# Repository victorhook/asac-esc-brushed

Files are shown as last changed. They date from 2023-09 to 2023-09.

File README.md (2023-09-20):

# **A** **S**imple **A**nd **C**ool brushed ESC
Why do cool fpv drones pretty much always use brushless motors? Well, because they are really good. BUT, they are quite expensive, and brushless ESCs are also quite expensive, since they require somewhat complex hardware and firmware. Thus, this project aims to make a simple and cool ESC that can be used for drones with *brushed* motors. Let's see how this goes!

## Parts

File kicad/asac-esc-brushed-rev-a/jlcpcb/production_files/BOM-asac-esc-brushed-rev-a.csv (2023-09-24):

Comment | Designator | Footprint | LCSC
470R | R9 | R_0402_1005Metric
RED | D7 | LED_0603_1608Metric
RED | D1 | LED_0603_1608Metric
AO3480C | Q1 | SOT-23
470R | R2 | R_0402_1005Metric
INA180A4IDBVR | U2 | SOT-23-5
STM32C011F6Px | U3 | TSSOP-20_4.4x6.5mm_P0.65mm
SD103AWS | D6 | D_SOD-323
AO3480C | Q4 | SOT-23
AO3480C | Q3 | SOT-23
10k | R3 | R_0402_1005Metric
2m | R1 | R_0805_2012Metric
SD103AWS | D8 | D_SOD-323
100n | C7 | C_0402_1005Metric
10u | C8 | C_0805_2012Metric
470R | R7 | R_0402_1005Metric
AO3480C | Q2 | SOT-23
10u | C3 | C_0805_2012Metric
SD103AWS | D4 | D_SOD-323
100n | C10 | C_0402_1005Metric
1k | R4 | R_0402_1005Metric
470R | R5 | R_0402_1005Metric
100n | C11 | C_0402_1005Metric
10k | R6 | R_0402_1005Metric
RED | D5 | LED_0603_1608Metric
1n | C2 | C_0402_1005Metric
10u | C1 | C_0805_2012Metric
4.7u | C6 | C_0603_1608Metric
FC JST 1.0mm Connector | J3 | JST_SHL_SM08B-SHLS-TF_1x08-1MP_P1.00mm_Horizontal
10u | C5 | C_0805_2012Metric
10u | C4 | C_0805_2012Metric
10k | R10 | R_0402_1005Metric
SD103AWS | D2 | D_SOD-323
RED | D3 | LED_0603_1608Metric
10u | C9 | C_0805_2012Metric
HT7533S | U1 | SOT-23-3
10k | R8 | R_0402_1005Metric

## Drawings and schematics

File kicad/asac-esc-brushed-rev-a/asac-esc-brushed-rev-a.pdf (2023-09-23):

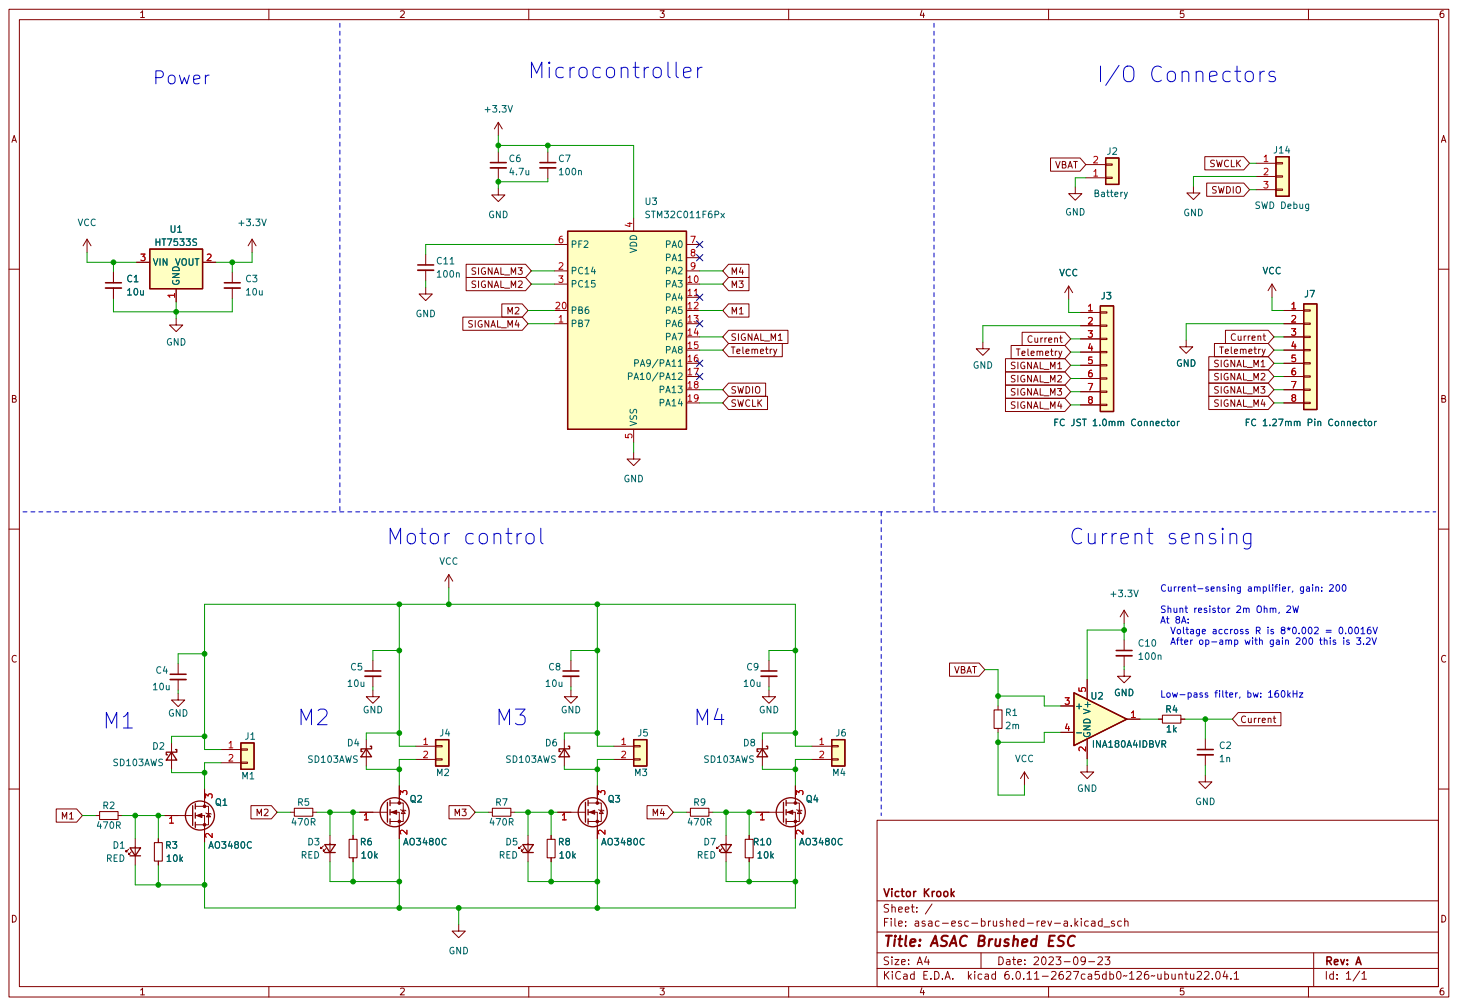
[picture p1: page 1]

J7 FC 1.27mm Pin Connector GND

File: asac-esc-brushed-rev-a.kicad_sch Sheet: / Victor Krook R2
D1 RED

Id: 1/1 Title: ASAC Brushed ESC

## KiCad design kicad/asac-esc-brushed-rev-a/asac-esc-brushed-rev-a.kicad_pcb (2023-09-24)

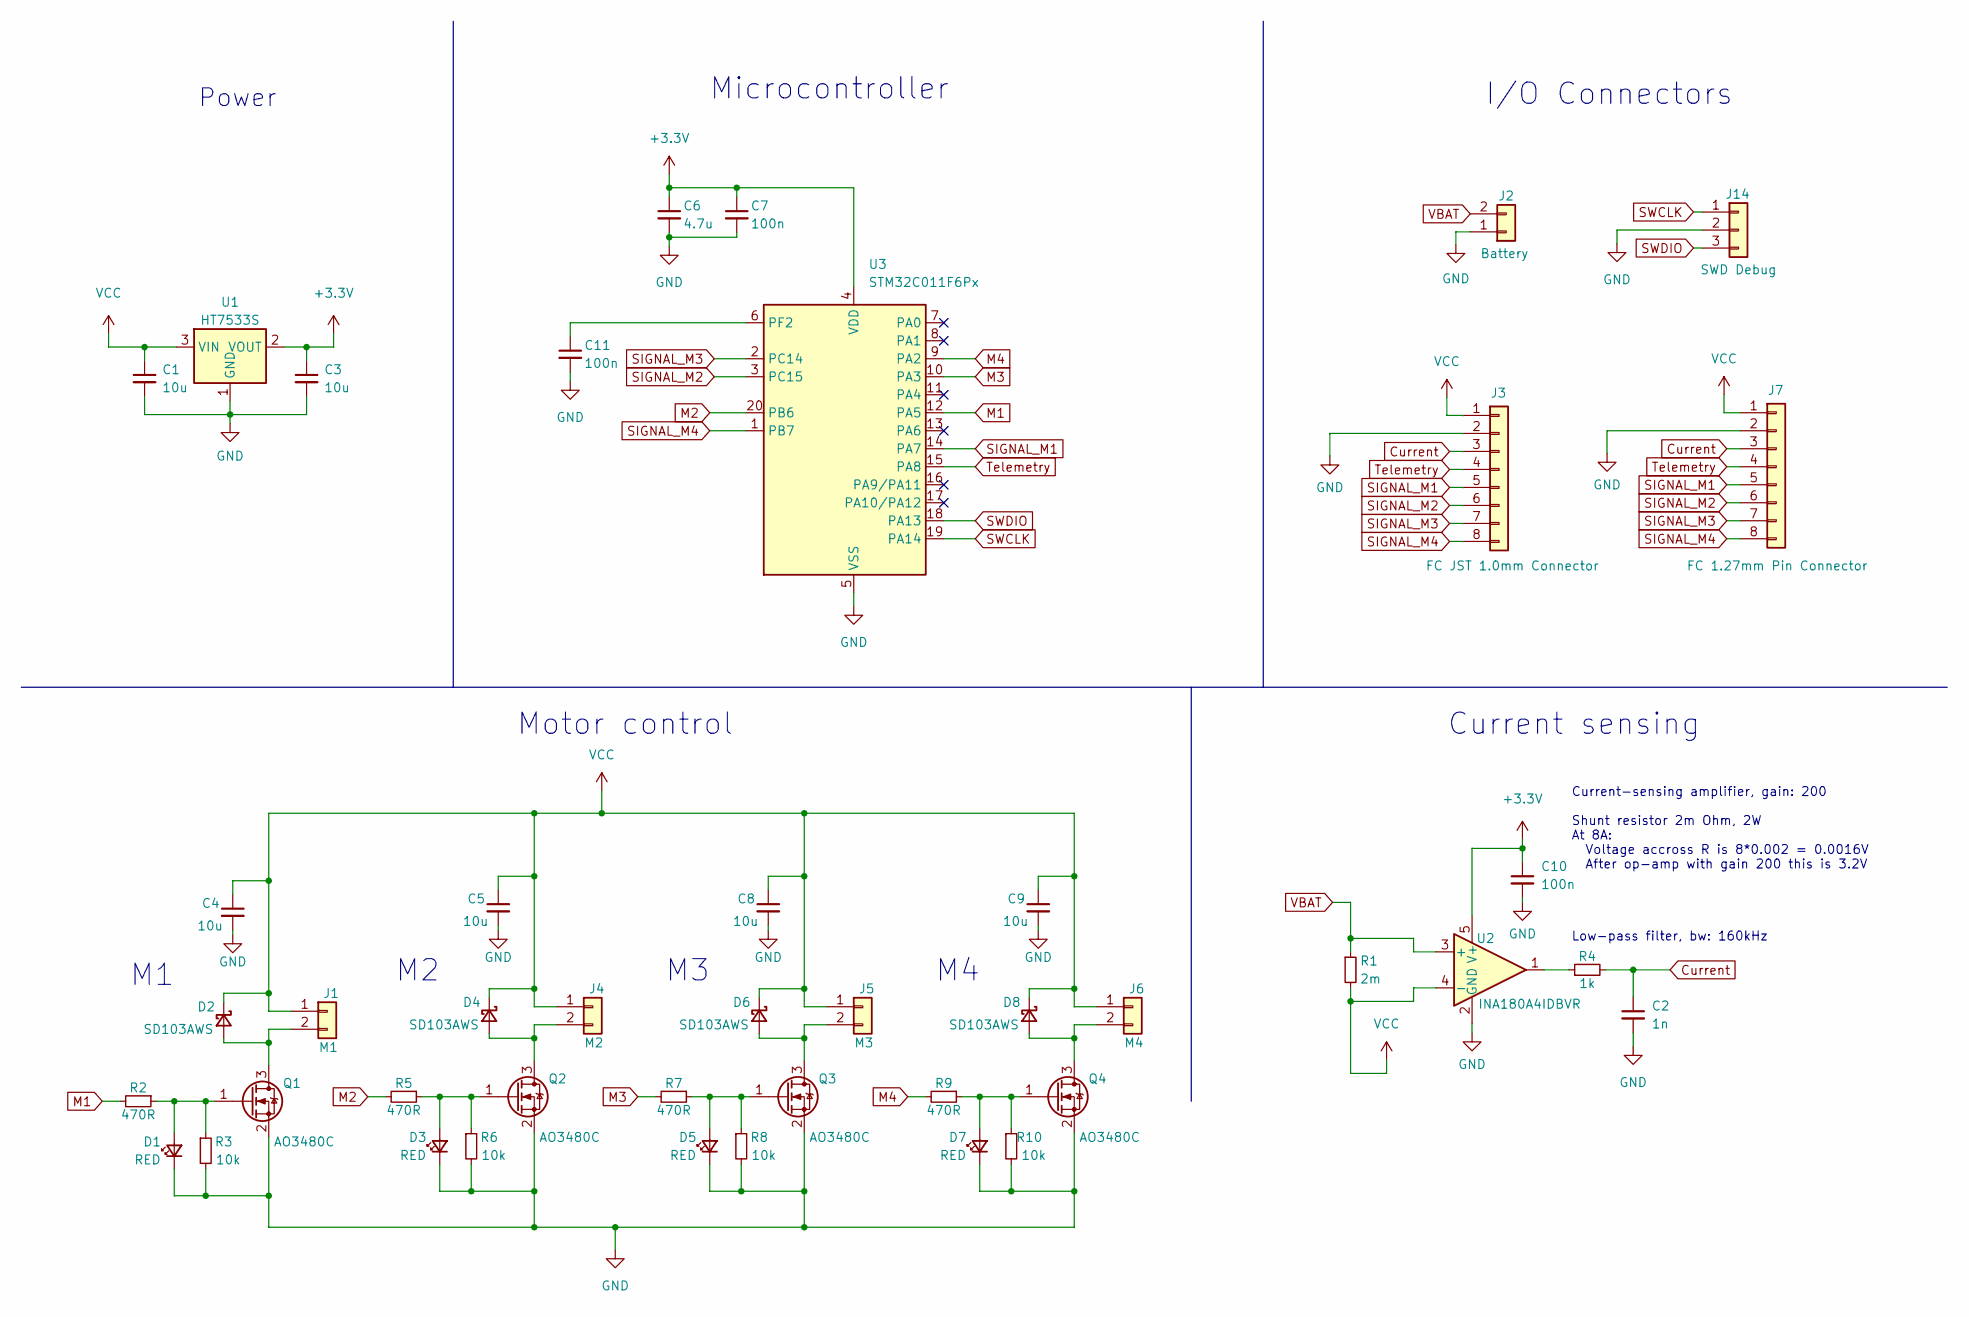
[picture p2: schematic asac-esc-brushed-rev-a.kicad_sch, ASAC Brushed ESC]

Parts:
C1, C3, C4, C5, C8, C9: 10u; C_0805_2012Metric
C2: 1n; C_0402_1005Metric
C6: 4.7u; C_0603_1608Metric
C7, C10, C11: 100n; C_0402_1005Metric
D1, D3, D5, D7: RED; LED_0603_1608Metric
D2: SD103AWS; D_SOD-323; MPN C2828423
D4, D6, D8: SD103AWS; D_SOD-323
J1: M1; Conn_01x02_VBAT_one_round
J2: Battery; Conn_01x02_VBAT_BIG
J3: FC JST 1.0mm Connector; JST_SHL_SM08B-SHLS-TF_1x08-1MP_P1.00mm_Horizontal
J4: M2; Conn_01x02_VBAT_one_round
J5: M3; Conn_01x02_VBAT_one_round
J6: M4; Conn_01x02_VBAT_one_round
J7: FC 1.27mm Pin Connector; PinHeader_1x08_P1.27mm_Vertical
J14: SWD Debug; PinHeader_1x03_P1.27mm_Vertical
Q1: AO3480C; SOT-23; MPN C188337
Q2, Q3, Q4: AO3480C; SOT-23
R1: 2m; R_0805_2012Metric
R2, R5, R7, R9: 470R; R_0402_1005Metric
R3, R6, R8, R10: 10k; R_0402_1005Metric
R4: 1k; R_0402_1005Metric
U1: HT7533S; SOT-23-3; MPN C347215
U2: INA180A4IDBVR; SOT-23-5; MPN C188337
U3: STM32C011F6Px; TSSOP-20_4.4x6.5mm_P0.65mm; MPN C5456198

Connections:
+3.3V: C3.1, C6.1, C7.1, C10.1, U1.2 (VOUT), U2.5 (V+), U3.4 (VDD)
Current: C2.1, J3.3, J7.3, R4.2
GND: C1.2, C2.2, C3.2, C4.2, C5.2, C6.2, C7.2, C8.2, C9.2, C10.2, C11.2, D1.1 (K), D3.1 (K), D5.1 (K), D7.1 (K), J2.1, J3.2, J7.2, J14.2, Q1.2 (S), Q2.2 (S), Q3.2 (S), Q4.2 (S), R3.2, R6.2, R8.2, R10.2, U1.1 (GND), U2.2 (GND), U3.5 (VSS)
M1: R2.2, U3.12 (PA5)
M2: R5.2, U3.20 (PB6)
M3: R7.2, U3.10 (PA3)
M4: R9.2, U3.9 (PA2)
unnamed: C11.1, U3.6 (PF2)
unnamed: D1.2 (A), Q1.1 (G), R2.1, R3.1
unnamed: D2.2 (A), J1.2, Q1.3 (D)
unnamed: D3.2 (A), Q2.1 (G), R5.1, R6.1
unnamed: D4.2 (A), J4.2, Q2.3 (D)
unnamed: D5.2 (A), Q3.1 (G), R7.1, R8.1
unnamed: D6.2 (A), J5.2, Q3.3 (D)
unnamed: D7.2 (A), Q4.1 (G), R9.1, R10.1
unnamed: D8.2 (A), J6.2, Q4.3 (D)
unnamed: R4.1, U2.1
SIGNAL_M1: J3.5, J7.5, U3.14 (PA7)
SIGNAL_M2: J3.6, J7.6, U3.3 (PC15)
SIGNAL_M3: J3.7, J7.7, U3.2 (PC14)
SIGNAL_M4: J3.8, J7.8, U3.1 (PB7)
SWCLK: J14.1, U3.19 (PA14)
SWDIO: J14.3, U3.18 (PA13)
Telemetry: J3.4, J7.4, U3.15 (PA8)
VBAT: J2.2, R1.1, U2.3 (+)
VCC: C1.1, C4.1, C5.1, C8.1, C9.1, D2.1 (K), D4.1 (K), D6.1 (K), D8.1 (K), J1.1, J3.1, J4.1, J5.1, J6.1, J7.1, R1.2, U1.3 (VIN), U2.4 (-)

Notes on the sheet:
Current sensing
Low-pass filter, bw: 160kHz
I/O Connectors
Power
Motor control
Current-sensing amplifier, gain: 200 Shunt resistor 2m Ohm, 2W At 8A: Voltage accross R is 8*0.002 = 0.0016V After op-amp with gain 200 this is 3.2V
Microcontroller

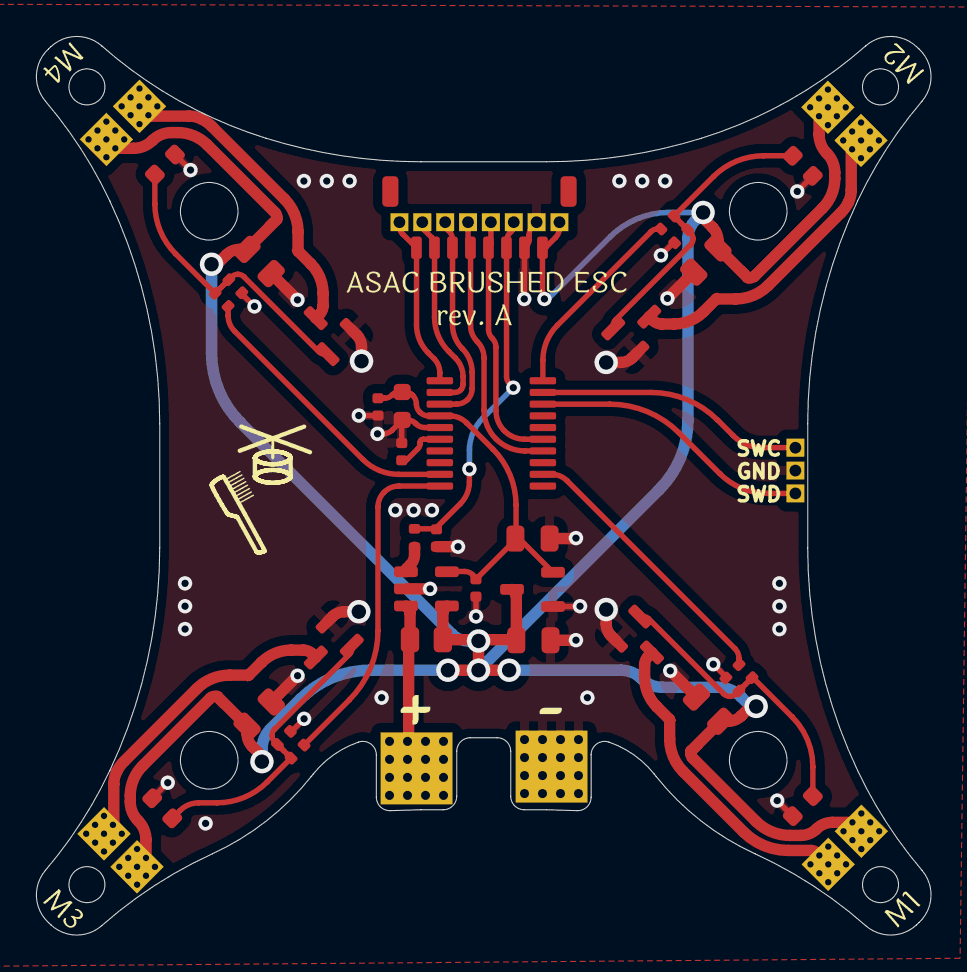
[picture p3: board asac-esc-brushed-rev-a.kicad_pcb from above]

Board: 2 copper layers, 49.7 x 49.9 mm, 44 parts (0 on the bottom side), 26 nets.

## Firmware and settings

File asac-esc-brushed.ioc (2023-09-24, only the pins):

Mcu.UserName=STM32C011F6Px
PA13.Signal=DEBUG_SWDIO
PA14-BOOT0.Signal=DEBUG_SWCLK
PA2.Signal=S_TIM1_CH3
PA3.Signal=S_TIM1_CH4
PA5.Signal=S_TIM1_CH1
PA7.Signal=GPIO_Input
PA8.Signal=USART2_TX
PB6.Signal=S_TIM1_CH2
PB7.Signal=GPIO_Input

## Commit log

2023-09-23 Finished rev A schematic, layout and routing
    All that is left now is to add some graphics!
    [asac-esc-brushed-rev-a.kicad_pcb, asac-esc-brushed-rev-a.kicad_sch]
2023-09-24 Added initial STM32CubeMX config
2023-09-24 Rev. A ready for order!
    [BOM-asac-esc-brushed-rev-a.csv, asac-esc-brushed-rev-a.kicad_pcb, asac-esc-brushed-rev-a.kicad_sch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]
